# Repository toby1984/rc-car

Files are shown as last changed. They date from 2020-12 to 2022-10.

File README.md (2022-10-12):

# RC car 

This project consists of a very crude "RC car" plus a 433 Mhz remote control (both driven by Arduino Nanos).

Since this is a fun project I didn't use any ready-made libraries at all (apart from the AVR libc) and the project builds with old-fashioned 'make' and does not use the Arduino IDE. You'll need a working linux avr-gcc installation and some ISP programmer to upload the firmware.

## Parts list

- some cardboard as base plate of the car (I had to glue together 2-3 layers to make it stiff enough)
- 2x Arduino Nano (~3€/pc)
- 1x 433 Mhz sender module with antenna (PCB has HFY-J1B printed on it, 1.40 €/pc))
- 1x 433 Mhz receiver module with antenna (RXB6 SuperHet, 2.50 €/pc)
- 2x helical 433 Mhz antenna ( 0.50€/pc)
- 2xAA battery holder  (~1€/pc)
- 4xAA battery holder (~1€/pc)
- 2x JGA25-370 6V DC motors, 133 RPM, with built-in encoders ( hard to find with encoders, ~11€/pc)
- 2x wheels, ball caster, 2x shaft coupling, 2x DC motor mounting brackets, screws (I bought a kit that included all of this plus 2 JGA25-370 motors for 15€, didn't use the motors though...)
- 2x 5V Step-Up/Step-Down converter (Pololu S9V11F5 , 4.79€/pc)
- 2-axis joystick module ( 3€/pc )
- DRV8833 module for driving the DC motors (3.00€/pc)

Total cost: A whopping 65€, ouch!

I think you can get this down to around ~40€ (go for cheaper motors without encoders,use no or lower-power step-up/step down converters and find cheap wheels, ball castermshaft couplings+mounting brackets) but given the fact that you can grab RC cars at your local toy store for much less it's obvious that this is never going to compete cost-wise.

## Radio remote pinout (Atmega328p)

The remote is designed to run on an ATPega328p with the radio module and joystick connected as follows:

### Joystick

X AXIS - ADC1
Y AXIS - ADC0

NOTE: Depending on the joystick you're using you might need to adjust the min/max and center values in joystick.c

### Radio

RF DATA OUT - D2

## RC car pinout (Atmega2560)

### Power

RC car will be powered as long as B0 stays HIGH.

### Radio

RF DATA IN - D7

### Motor driver

Wiring:

ORANGE (IN1),YELLOW (IN2) -> Left motor
RED (IN3),GREEN (IN4) -> Right motor

Pinout:
Left motor: OC0A and OC0B
Right motor: OC2A and OC2B

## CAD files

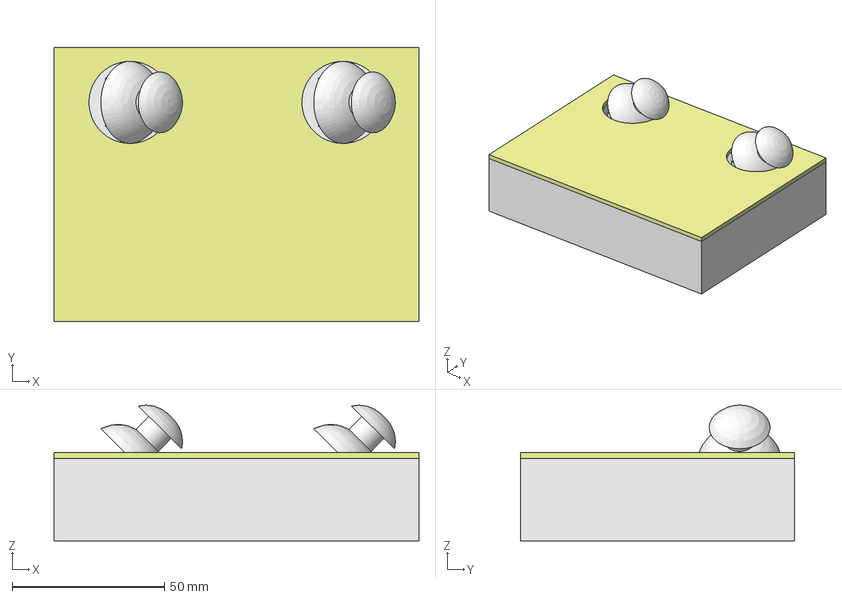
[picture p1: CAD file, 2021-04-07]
case_cad/case.FCStd
120.0 x 90.0 x 44.6 mm
case_bottom
joy_left_orig
joy_right_cloned
case_top
power pcb
battery_holder
arduino_nano

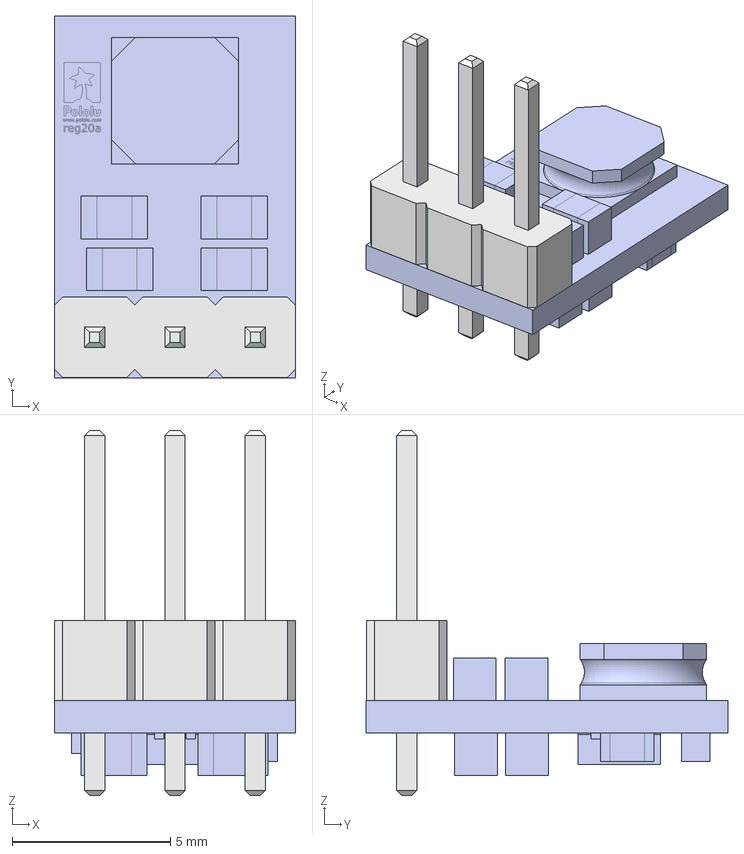
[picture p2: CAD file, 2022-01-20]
pcb_control/test.FCStd
7.62 x 11.4 x 11.5 mm
pololu-5v-step-up-step-down-voltage-regulator-s9v11f5
PinHeader_1x03_P254mm_Vertical

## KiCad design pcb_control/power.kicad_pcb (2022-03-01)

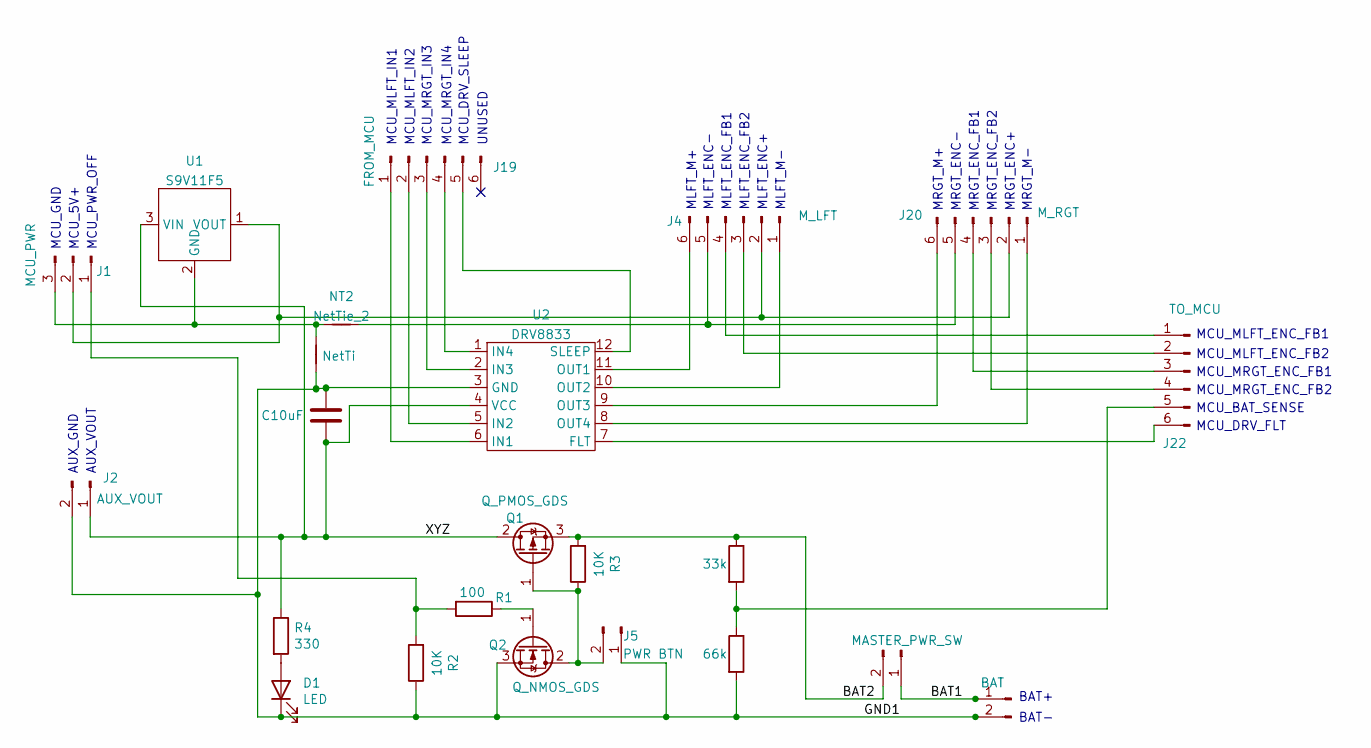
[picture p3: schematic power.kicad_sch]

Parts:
C1: C10uF; C_Radial_D5.0mm_H11.0mm_P2.00mm
D1: LED; LED_D5.0mm
J1: MCU_PWR; JST_XH_B3B-XH-A_1x03_P2.50mm_Vertical
J2: AUX_VOUT; JST_XH_B2B-XH-A_1x02_P2.50mm_Vertical
J4: M_LFT; JST_XH_S6B-XH-A_1x06_P2.50mm_Horizontal
J5: PWR BTN; JST_XH_B2B-XH-A_1x02_P2.50mm_Vertical
J6: MASTER_PWR_SW; JST_XH_B2B-XH-A_1x02_P2.50mm_Vertical
J19: FROM_MCU; JST_XH_B6B-XH-A_1x06_P2.50mm_Vertical
J20: M_RGT; JST_XH_S6B-XH-A_1x06_P2.50mm_Horizontal
J21: BAT; JST_XH_S2B-XH-A-1_1x02_P2.50mm_Horizontal
J22: TO_MCU; JST_XH_B6B-XH-A_1x06_P2.50mm_Vertical
NT1: NetTi; NetTie-2_SMD_Pad2.0mm
NT2: NetTie_2; NetTie-2_SMD_Pad2.0mm
Q1: Q_PMOS_GDS; TO-220-3_Vertical
Q2: Q_NMOS_GDS; TO-220-3_Vertical
R1: 100; R_Axial_DIN0207_L6.3mm_D2.5mm_P10.16mm_Horizontal
R2, R3: 10K; R_Axial_DIN0207_L6.3mm_D2.5mm_P10.16mm_Horizontal
R4: 330; R_Axial_DIN0207_L6.3mm_D2.5mm_P10.16mm_Horizontal
R5: 33k; R_Axial_DIN0207_L6.3mm_D2.5mm_P10.16mm_Horizontal
R6: 66k; R_Axial_DIN0207_L6.3mm_D2.5mm_P10.16mm_Horizontal
U1: S9V11F5; pololu_5v_updown
U2: DRV8833; drv8833

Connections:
/BAT1: J6.1, J21.1
/BAT2: J6.2, Q1.3 (S), R3.2, R5.1
/GND1: C1.1, D1.1 (K), J2.2, J5.1, J21.2, NT1.1, Q2.3 (S), R2.1, R6.2, U2.3 (GND)
/XYZ: C1.2, J2.1, Q1.2 (D), R4.1, U1.3 (VIN), U2.4 (VCC)
unnamed: D1.2 (A), R4.2
unnamed: J1.1, R1.2, R2.2
unnamed: J1.2, J4.2, J20.2, U1.1 (VOUT)
unnamed: J1.3, NT1.2, NT2.1, U1.2 (GND)
unnamed: J4.1, U2.10 (OUT2)
unnamed: J4.6, U2.11 (OUT1)
unnamed: J5.2, Q1.1 (G), Q2.2 (D), R3.1
unnamed: J19.1, U2.6 (IN1)
unnamed: J19.2, U2.5 (IN2)
unnamed: J19.3, U2.2 (IN3)
unnamed: J19.4, U2.1 (IN4)
unnamed: J19.5, U2.12 (SLEEP)
unnamed: J20.1, U2.8 (OUT4)
unnamed: J20.3, J22.4
unnamed: J20.4, J22.3
unnamed: J4.5, J20.5, NT2.2
unnamed: J20.6, U2.9 (OUT3)
unnamed: J4.4, J22.1
unnamed: J4.3, J22.2
unnamed: J22.5, R5.2, R6.1
unnamed: J22.6, U2.7 (FLT)
unnamed: Q2.1 (G), R1.1

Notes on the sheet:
MCU_MRGT_ENC_FB1
MCU_MRGT_IN3
MRGT_ENC_FB1
MCU_PWR_OFF
MCU_DRV_FLT
UNUSED
MRGT_ENC-
MLFT_ENC_FB2
BAT-
AUX_VOUT
MLFT_ENC_FB1
MLFT_M-
MLFT_ENC-
MLFT_M+
MCU_5V+
MCU_MLFT_IN2
MRGT_M+
MLFT_ENC+
MCU_MRGT_IN4
MCU_MLFT_ENC_FB2
MCU_BAT_SENSE
MCU_MRGT_ENC_FB2
MCU_MLFT_IN1
MCU_GND
MRGT_M-
AUX_GND
MRGT_ENC_FB2
MRGT_ENC+
MCU_DRV_SLEEP
BAT+
MCU_MLFT_ENC_FB1

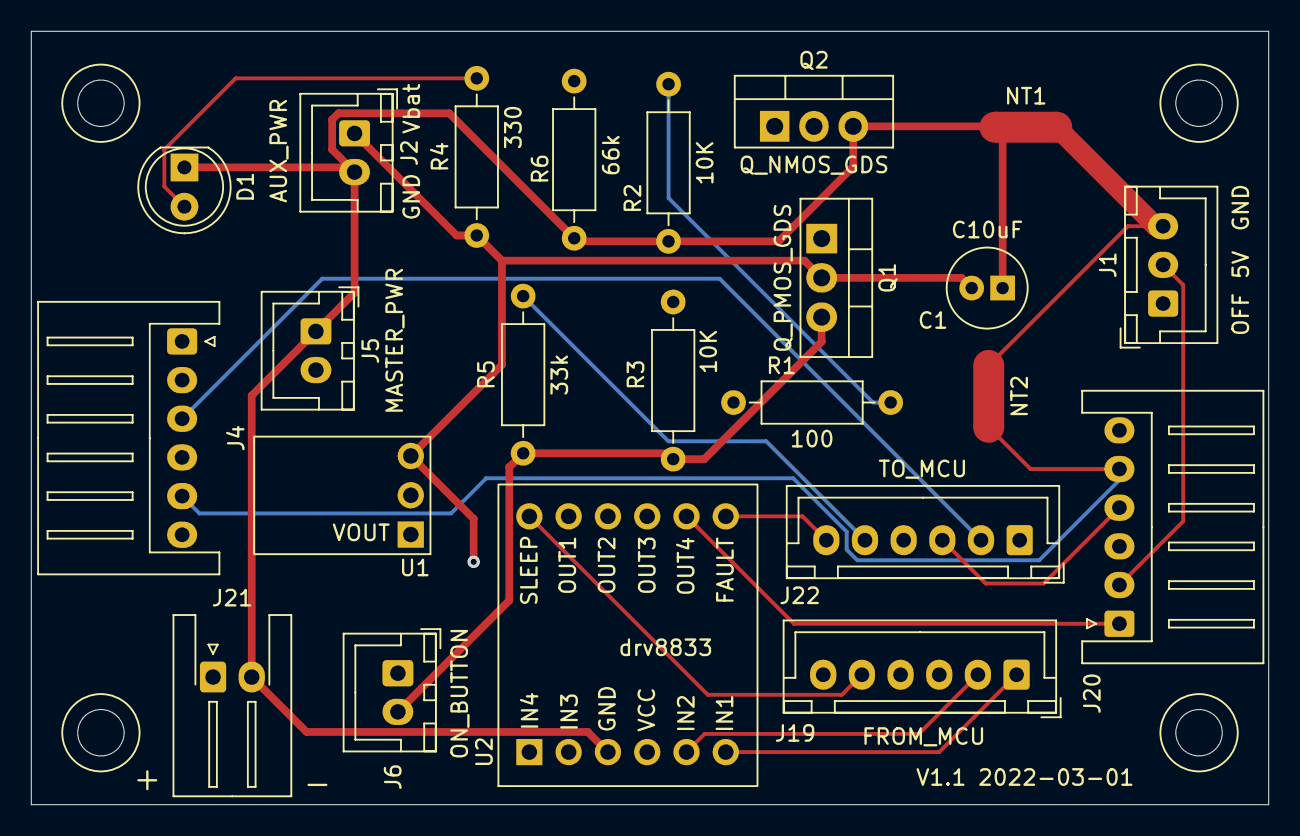
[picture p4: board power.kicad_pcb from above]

Board: 4 copper layers, 80.0 x 50.0 mm, 23 parts (0 on the bottom side), 26 nets.

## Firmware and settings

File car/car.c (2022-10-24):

#include <avr/io.h>
#include <stdlib.h>
#include <util/delay.h>
#include <avr/interrupt.h>
#include "radio_receiver.h"
#include "uart.h"
#include "crc.h"
#include "watchdog.h"
#include "pid.h"
#include "encoder.h"

#define WATCHDOG_TIMEOUT_SECONDS 30
#define WATCHDOG_DISABLED
#define DEBUG

#define DEBUG_PIN _BV(5) // PB5

#define MOTOR_LEFT_DIR _BV(2)
#define MOTOR_LEFT_DIR_DDR DDRD
#define MOTOR_LEFT_DIR_REG PORTD

#define MOTOR_RIGHT_DIR _BV(3)
#define MOTOR_RIGHT_DIR_DDR DDRD
#define MOTOR_RIGHT_DIR_REG PORTD

// maximum speed difference (in percent) between both
// motors while turning and moving forwards / backwards at the same time
// this ultimately defines how fast you're able to turn when not stationary
#define MAX_MOTOR_SPEED_DIFF 0.5

// MCU will only be powered as long as
// POWER_UP_PIN is HIGH
#define POWER_UP_PIN 6
#define POWER_UP_DDR DDRL
#define POWER_UP_PORT PORTL

enum direction {
	FORWARD,BACKWARD,STOP
};

enum direction leftDir;
enum direction rightDir;

pid_data left_motor_pid;
pid_data right_motor_pid;

void mcu_power_on() {
      POWER_UP_DDR |= (1<<POWER_UP_PIN);
      POWER_UP_PORT |= (1<<POWER_UP_PIN);
}

void mcu_power_off() {
      POWER_UP_DDR |= (1<<POWER_UP_PIN);
      POWER_UP_PORT &= ~(1<<POWER_UP_PIN);
}

void motor_init() {

    // initialize PID controllers
    pid_init(&left_motor_pid,0,0,0);
    pid_init(&right_motor_pid,0,0,0);

    // setup two timers for counting motor encoder
    // events.
    // 8 bit counters are enough since the motors & voltages I'm using
    // yields at most ~1300 ticks per second and
    // I'm going to update the PID controllers with the current tick rate
    // every 25 ms so I expected at most 1300 / (1000ms / 25ms) => ~33 ticks per sample

    MOTOR_LEFT_DIR_DDR |= MOTOR_LEFT_DIR;
    MOTOR_RIGHT_DIR_DDR |= MOTOR_RIGHT_DIR;
        
    // enable output pins for left motor
    // Atmega2560: (OC0A = PB7, OC0B = PG5)

	DDRB |= (1<<7);
	DDRG |= (1<<5);

    // enable output pins for right motor
    // Atmega2560: (OC2A = PB4 , OC2B = PH6)
    DDRB |= (1<<4);
    DDRH |= (1<<6);

	leftDir = STOP;
	rightDir = STOP;
}

void motor_left_stop() {

#ifdef DEBUG
	uart_print("\r\nMotor left: STOP");
#endif
    TCCR0B &= ~(1<<CS02|1<<CS01|1<<CS00);
    TCCR0A &= ~(1<<COM0A1 | 1<<COM0A0 | 1<<COM0B1 | 1<<COM0B0 );  
  
	PORTB &= ~(1<<7);
	PORTG &= ~(1<<5);
    
	leftDir = STOP;
}

void motor_right_stop() {

#ifdef DEBUG
	uart_print("\r\nMotor right: STOP");
#endif
    TCCR2B &= ~(1<<CS22|1<<CS21|1<<CS20);
    TCCR2A &= ~(1<<COM2A1 | 1<<COM2A0 | 1<<COM2B1 | 1<<COM2B0 );  
  
    PORTB &= ~(1<<4);
    PORTH &= ~(1<<6);
    
	rightDir = STOP;
}

void motor_left_start(enum direction newDir, uint8_t newDuty ) {

    // left motor (OC0A = PD6 , OC0B = PD5
	uint8_t pwm = (0xff * newDuty) / 100.0;

#ifdef DEBUG
	uart_print("\r\nMotor left: direction=");
	uart_putdecimal(newDir);
    uart_print(" , duty ");
	uart_putdecimal(newDuty);
	uart_print(" (pwm");
	uart_putdecimal(pwm);
	uart_print(")");		
#endif	
  
    if ( newDir == FORWARD ) { 
        // 0C0A = pwm , OC0B = 1
		OCR0A = pwm;					
		PORTG |=  (1<<5);

        TCCR0A &= ~(1<<COM0A1 | 1<<COM0A0 | 1<<COM0B1 | 1<<COM0B0 );  
        TCCR0A |=  (1<<WGM00  | 1<<COM0A1 | 1<<COM0A0 );        		
    } else { 
    	// 0C0A = 1 , OC0B = pwm
		OCR0B = pwm;
		PORTB |=  (1<<7);
	
        TCCR0A &= ~(1<<COM0A1 | 1<<COM0A0 | 1<<COM0B1 | 1<<COM0B0 );  
        TCCR0A |=  (1<<WGM00  | 1<<COM0B1 | 1<<COM0B0 );  		
    }

    TCCR0B |= 1<<CS00; // CPU_FREQ / 1	    
      
	leftDir = newDir;
}

void motor_right_start(enum direction newDir, uint8_t newDuty ) {

    // right motor (OC2A , OC2B)
	uint8_t pwm = (0xff * newDuty) / 100.0;

#ifdef DEBUG
	uart_print("\r\nMotor right: direction=");
	uart_putdecimal(newDir);
    uart_print(" , duty ");
	uart_putdecimal(newDuty);
	uart_print(" (pwm");
	uart_putdecimal(pwm);
	uart_print(")");
#endif
  
    if ( newDir == FORWARD ) { 
        // 0C2A = pwm , OC2B = 1
		OCR2A = pwm;					
		PORTH |=  (1<<6);

        TCCR2A &= ~(1<<COM2A1 | 1<<COM2A0 | 1<<COM2B1 | 1<<COM2B0 );  
        TCCR2A |=  (1<<WGM20  | 1<<COM2A1 | 1<<COM2A0 );        		
    } else { 
    	// 0C2A = 1 , OC2B = pwm
		OCR2B = pwm;
		PORTB |=  (1<<4);
	
        TCCR2A &= ~(1<<COM2A1 | 1<<COM2A0 | 1<<COM2B1 | 1<<COM2B0 );  
        TCCR2A |=  (1<<WGM20  | 1<<COM2B1 | 1<<COM2B0 );  		
    }

    TCCR2B |= 1<<CS20; // CPU_FREQ / 1	    
      
	rightDir = newDir;
}

void motor_change(enum direction newLeftDir,enum direction newRightDir, uint8_t newDutyLeft, uint8_t newDutyRight) {

    // TODO: Maybe stop both 8-bit timers if any of the outputs needs to change and 
    //       start them at the same time ?
	if ( newLeftDir == STOP ) {
		motor_left_stop();
	} else {
		motor_left_start(newLeftDir, newDutyLeft);
	}
	if ( newRightDir == STOP ) {
		motor_right_stop();
	} else {
		motor_right_start(newRightDir, newDutyRight);
	}	
}

uint8_t msg_size_calculator(uint8_t first_byte) {
	// TODO: Implement this based on message type, see protocol.h
	return 3;
}

int8_t clamp(int8_t input) {
    return input < -100 ? -100 : input > 100 ? 100 : input;
}

void watchdog_irq() {
    mcu_power_off();
}

// careful, this is an interrupt handler...
void encoder_callback(uint16_t ticksLeftMotor, uint16_t ticksRightMotor) {
 #ifdef DEBUG
 	uart_print("\r\n*** Encoders left/right: ");
    uart_putdecimal( ticksLeftMotor );
 	uart_print("/ ");
    uart_putdecimal( ticksRightMotor );
 	uart_print("\r\n");
 #endif
}

void main() {

	uint8_t msg[3];

    // change pin to HIGH as the
    // very first action here so
    // MCU stays powered
    mcu_power_on();

 	DDRC |= (1<<2) | (1<<3); // HMMMM... what's this for ? delete ?

  #if defined(DEBUG) || defined(DEBUG_IR)
      uart_init();
  #endif	

 	motor_init();
 	radio_receiver_init();

    enc_init(1000, &encoder_callback);

 #ifdef DEBUG
 	uart_print("online 2");
 #endif	

#ifndef WATCHDOG_DISABLED
    watchdog_start( watchdog_irq, WATCHDOG_TIMEOUT_SECONDS );
#endif

 	while (1) {
        msg[0]=0;
        msg[1]=0;
 		int8_t received = radio_receive(&msg[0],msg_size_calculator);
 		if ( received == 3 && crc8(&msg[0],3) == 0 ) 
 		{
#ifdef DEBUG
 			// uint32_t value = (uint32_t) msg[0] << 16 | (uint32_t) msg[1] << 8 | (uint32_t) msg[2];
 			// uart_puthex( value );
#endif

 			int8_t xDir = msg[0];
 			int8_t yDir = msg[1];

#ifdef DEBUG
 			uart_print("\r\n(");
 			uart_putsdecimal(xDir);
 			uart_print("/");
 			uart_putsdecimal(yDir);
 			uart_print(")");
#endif

			xDir = clamp(xDir);
			yDir = clamp(yDir);

 			if ( yDir == 0 ) {
 				if ( xDir == 0 ) {
 					// full stop
 					motor_change(STOP,STOP, 0, 0);
 				} else if ( xDir < 0 ) {
 					// turn left in-place (left motor backwards, right motor forwards)
 					motor_change(BACKWARD,FORWARD, -xDir, -xDir );
#ifndef WATCHDOG_DISABLED
                    watchdog_reset();
#endif
 				} else {
 					// turn right in-place (left motor forwards, right motor backwards)
 					motor_change(FORWARD,BACKWARD, xDir, xDir );
#ifndef WATCHDOG_DISABLED
                    watchdog_reset();
#endif
 				}
 			} else if ( xDir == 0 ) {
 				// yDir != 0 , xDir == 0 
                watchdog_reset();
 				if ( yDir > 0 ) {
 					// forwards		
					motor_change(FORWARD,FORWARD, yDir, yDir );
 				} else {
 					// backwards
					motor_change(BACKWARD,BACKWARD, -yDir, -yDir );  					
 				}
 			} else {
 				// yDir != 0 , xDir != 0 
                watchdog_reset();
 				enum direction dir = yDir > 0 ? FORWARD : BACKWARD;
 				if ( xDir < 0 ) {
 					// turn left while driving forward -> left motor must run SLOWER than right motor
 					float delta = 1.0 - MAX_MOTOR_SPEED_DIFF*(-xDir/100.0);
					motor_change(dir, dir, yDir*delta , yDir ); 
 				}  else {
 					// turn right while driving forward -> right motor must run SLOWER than left motor
					float delta = 1.0 - MAX_MOTOR_SPEED_DIFF*(xDir/100.0); 						
					motor_change(dir, dir, yDir, yDir*delta ); 						
 				}
 			}
 		}
 	}
}

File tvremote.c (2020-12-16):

// #define __AVR_ATmega88PB__
#include <avr/io.h>
#include <stdlib.h>
#include <util/delay.h>
#include <avr/interrupt.h>
#include "uart.h"
#include "joystick.h"

#define DEBUG
// #define DEBUG_IR
#define DEBUG_PIN _BV(5) // PB5
#define MOTOR_LEFT _BV(4) // PB4
#define MOTOR_RIGHT _BV(3) // PB3
#define IR_IN 6 // PD6

#define IR_KEY_FORWARD 0x00ffa05f
#define IR_KEY_BACKWARD 0x00ff40bf
#define IR_KEY_LEFT 0x00ff50af
#define IR_KEY_RIGHT 0x00ff7887
#define IR_KEY_STOP 0x00ff02fd

#define RIGHT_MOTOR_SPD_ADJUST_FWD 0.87
#define RIGHT_MOTOR_SPD_ADJUST_BWD 0.75

enum direction {
	FORWARD,BACKWARD,STOP
};

volatile uint8_t is_moving;

enum direction leftDirection;
enum direction rightDirection;

// duty cycle in milliseconds, left motor
uint16_t dutyLeftMillis;
// duty cycle in milliseconds, right motor
uint16_t dutyRightMillis;

#define ICR1_VALUE 19999 // 50 hz at prescaler = F_CPU/8

void motor_speed_changed();

void start_pwm() {

    TCCR1A |= 1<<WGM11 | 1<<COM1A1 | 1<<COM1A0 | 1<<COM1B1 | 1<<COM1B0;
    TCCR1B |= 1<<WGM13 | 1<<WGM12 | 1<<CS11; // prescaler = 1/8

	ICR1 = ICR1_VALUE; // 50 hz at prescaler = F_CPU/8

	OCR1A = ICR1_VALUE - dutyLeftMillis; 
	OCR1B = ICR1_VALUE - dutyRightMillis;

	DDRB |= 1<<1 | 1<<2; // PB1 (OCR1A) and PB2 (OCR1B)
}

void motor_init() {

    is_moving = 0;

	leftDirection = STOP;
	rightDirection = STOP;

	dutyLeftMillis = 0;
	dutyRightMillis = 0;

	start_pwm();
}

void change_direction(char newDir) {

    enum direction oldLeft = leftDirection;
    enum direction oldRight = rightDirection;

	switch( newDir ) {
		case 'x':    
			leftDirection = STOP;
			rightDirection = STOP;       
			break;
		case 'w':    
			if ( leftDirection == BACKWARD && rightDirection == BACKWARD ) {
				leftDirection = STOP;
				rightDirection = STOP;     			
			} else {
				leftDirection = FORWARD;
				rightDirection = FORWARD;  
			}    
			break;
		case 's':
			if ( leftDirection == FORWARD && rightDirection == FORWARD) {
				leftDirection = STOP;
				rightDirection = STOP;    				 			
			} else {
				leftDirection = BACKWARD;
				rightDirection = BACKWARD;  
			} 		  
			break;      
		case 'a':
			leftDirection = BACKWARD;
			rightDirection = FORWARD;
			break;
		case 'd':
			leftDirection = FORWARD;
			rightDirection = BACKWARD;    
		break;
	}

	if ( oldLeft != leftDirection || oldRight != rightDirection ) {
		is_moving = leftDirection != STOP || rightDirection != STOP;
		switch(leftDirection) {
			case FORWARD:
				dutyLeftMillis = 1000; // 1ms high pulse
	          	break; 
	      	case STOP:
	      		dutyLeftMillis = 0;
	          	break;
	      	case BACKWARD:
	      	    dutyLeftMillis = 2000; // 2 ms high pulse
	     		break; 
	     }
	 	switch(rightDirection) {
	 		case FORWARD:
	 			dutyRightMillis = 2000*RIGHT_MOTOR_SPD_ADJUST_FWD;
	     		break; 
	 		case STOP:
	     		dutyRightMillis = 0;
	     		break;
	 		case BACKWARD:
	     		dutyRightMillis = 1000*RIGHT_MOTOR_SPD_ADJUST_BWD;
	     		break; 
	 	}
	 	motor_speed_changed();
 	}
}

void motor_speed_changed() {

#ifdef DEBUG
	uart_print("\r\nDuty cycles: left = ");
	uart_putdecimal(dutyLeftMillis);
	uart_print(" , right = ");
	uart_putdecimal(dutyRightMillis);	
#endif
	OCR1A = ICR1_VALUE - dutyLeftMillis; //18000
	OCR1B = ICR1_VALUE - dutyRightMillis; //18000	
}

void ir_init() {
	cli();
  // let INT1 be triggered by falling edge,
  // which marks the beginning of an IR transmission
	EICRA = (EICRA & ~(_BV(ISC11) | _BV(ISC10))) | _BV(ISC11);
	EIMSK |= _BV(INT1);
	sei();
}

#define MAX_IR_BITS 48
uint32_t lastResult;
uint16_t ir_rec_high[MAX_IR_BITS];
uint16_t ir_rec_low[MAX_IR_BITS];

// invoked at start of IR transmission (PD6 falling edge)
ISR(INT1_vect) {
	uint16_t counter;
	uint8_t bitCount = 0;
	while(1) { 
    // Wait for PD6 to become HIGH again    
    // NOTE: Signal from IR sensor is inverted to LOW input 
    //       is logical HIGH
		counter = 65535;
		while ( !(PIND & _BV(IR_IN)) && --counter > 0) {    
		}
		if ( counter == 0 ) {
			break;
		}      
		ir_rec_high[bitCount] = 65535-counter;
    // pin is high, start counting while waiting for pin to go low again
		counter = 65535;
		while ( PIND & _BV(IR_IN) && --counter > 0) {    
		}
		if ( counter == 0 ) {
			break;
		}    
		ir_rec_low[bitCount++] = 65535-counter;
		if ( bitCount == MAX_IR_BITS ) {
			break;
		}
	}

	if ( bitCount > 0 ) {

#ifdef DEBUG_IR
		uart_print("\r\n-------------\r\n");
		for ( uint8_t i = 0 ; i < bitCount ; i++ ) {
			uart_print("bit ");
			uart_putdecimal( i );
			uart_print(": ");        
			uart_putdecimal( ir_rec_high[i] );
			uart_print(" HIGH, ");  
			uart_putdecimal( ir_rec_low[i] );
			uart_print(" LOW\r\n");
		}
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

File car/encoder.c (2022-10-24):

#include "encoder.h"
#include <stdint.h>
#include "avr/interrupt.h"
#include "avr/io.h"
#include "uart.h"

#define DEBUG
/*
 * TIMER USAGE:
 *
 * 8-bit timer/counter0  (UNUSED)
 * 16-bit timer/counter1 (radio)
 * 8-bit timer/counter2  (UNUSED)
 * 16-bit timer/counter3 (read encoder pulse counters and invoke callback to adjust motor speed)
 * 16-bit timer/counter4 (counts encoder impulses left motor)
 * 16-bit timer/counter5 (counts encoder impulses right motor)
 */

static volatile encoder_handler encoder_handler_callback;

static uint8_t prescaler_bitmask;

inline static void enc_reset_counters() {
    TCNT4 = 0;
    TCNT5 = 0;
}

static void enc_stop() {
	TCCR3B &= ~( _BV(CS12) | _BV(CS11) | _BV(CS10) );
}

static void enc_start() {
    TIFR3 |= (1<<OCF1A); // clear overflow marker bit
	TCCR3B = (TCCR3B & ~( _BV(CS12) | _BV(CS11) | _BV(CS10) ) ) | prescaler_bitmask;

    // setup timers 4 & 5 as counters
    enc_reset_counters();

    TCCR4B = 0;
	TCCR4B = (TCCR4B & ~( _BV(CS42) | _BV(CS41) | _BV(CS40) ) ) | 6; // CSn2:0 = 6 -> Trigger on rising edge of Tn
	TCCR5B = 0;
	TCCR5B = (TCCR5B & ~( _BV(CS52) | _BV(CS51) | _BV(CS50) ) ) | 6; // CSn2:0 = 6 -> Trigger on rising edge of Tn
}

uint8_t enc_init(float samplingIntervalMillis, encoder_handler callback)
{
    // calculate 16-bit timer TOP value and PRESCALER
    // based on current CPU frequency and the desired sampling samplingIntervalMillis

    uint16_t available_opts[5] = {1,8,64,256,1024};
    uint8_t prescaler_idx = 0;
    uint32_t top = (samplingIntervalMillis/1000.0f) * ( (float) F_CPU / available_opts[ prescaler_idx ]);
    while ( top > 65535 && prescaler_idx < 4 ) {
        prescaler_idx++;
        top = (samplingIntervalMillis/1000.0f) * ( (float) F_CPU / available_opts[ prescaler_idx] );
    }

#ifdef DEBUG
 	uart_print("\r\nTOP: ");
  	uart_putdecimal( top );
    uart_print("\r\n");
 #endif

    if ( top > 65535 ) {
        return 1;
    }

#ifdef DEBUG
 	uart_print("\r\nPRESCALER 2: ");
 	uart_putdecimal(available_opts[prescaler_idx]);
 #endif

    prescaler_bitmask = 1 + prescaler_idx;

    cli();

    OCR3AH = ( top >> 8 ) & 0xff;
    OCR3AL = ( top & 0xff );

    encoder_handler_callback = callback;

    // enable IRQ on COMPARE A MATCH
    TIMSK3 |= (1<<OCIE3A);

    // enable interrupts
    enc_start();
    sei();

    return 0; // success
}

ISR(TIMER3_COMPA_vect)
{
    uint16_t left = TCNT4;
    uint16_t right = TCNT5;

    enc_reset_counters();
    encoder_handler_callback( left, right );
}

void enc_reset()
{
    enc_stop();
    enc_start();
}

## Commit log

2021-01-13 added support for having 16-bit timer trigger an IRQ after a specific microseconds interval
2021-01-13 started work on I2C to have a second arduino perform the radio communication
2021-02-01 added KiCAD files
    [power.kicad_pcb, power.sch]
2021-04-07 added case FreeCad
    [case.FCStd]
2021-07-31 fixed X/Y axis mapping calculation in joystick.c
    [joystick.c, remote.c]
2021-08-02 added support for automatically powering down after 2 minutes
2021-08-19 re-wrote I2C sending to be interrupt-driven
2022-06-06 adjusted ADC max value, for some reason the ADC does not reach the 1023 maximum reading
